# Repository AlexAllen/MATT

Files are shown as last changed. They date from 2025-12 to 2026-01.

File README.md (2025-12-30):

# Overview

MATT stands for "Multifunction Altimeter with Telemetry and Tracking", and is a DIY flight computer project that aims to tick several boxes in the [United Kingdom Rocketry Association's (UKRA) Model Achievement Program (MAP)](https://ukra.org.uk/certification/model-achievement-programme/). I have already done the DIY altimeter task, using an Arduino and breakout boards on stripboard, as recorded in [my rocket altimeter repo](https://github.com/AlexAllen/rocket_altimeter), and this project intends to produce something that can tick all of the remaining MAP tasks that require a custom altimeter:

* DIY flight computer
	* Details are light on the exact requirements, but I'm assuming a typical dual deploy flight computer
* Satellite
	* A cansat which records some physical data and transmits it back to the ground at 1Hz.
* Land under thrust
	* Need to be able to control servos for thrust vectoring

I also want to use this project as a vehicle for learning about PCB design, and to improve my electronics skills more generally. I intend to use a microcontroller board (maybe a Pico of some sort, or a Teensy) as a starting point, and then to create my own PCB to provide the rest of the functionality I require. I might do this in stages, creating some simpler boards with a subset of the final functionality on the way towards the final board. 

While the resulting flight computer will be overkill for any of these applications, as I don't expect space or weight contraints to be an issue for any of the flights (within reason), having them all use the same computer (or at least a subset of the same computer) means that every flight can help collect data and test functionality for each of the other applications. If I subsequently find I want a more compact, focussed flight computer for a specific application, then that can be its own project, building on the experience gained here. 

---------------------

# Requirements

1. Must have Mach safe two channel (apogee and main) deployment triggered off pressure data
	* Required to meet DIY flight computer task definition
1. Must have buzzer for audible altimeter arming alerts
	* Required for safety when completing DIY flight computer task
1. Must record flight data in a robust way in flight (not to an SD card!), and make the data retrievable afterwards
	* Will make the result more useful, and make it easier to test
1. Could have individual wireless test functionality for both deployment channels
	* Makes the result more flexible, but could be a later update
1. Must have UK legal radio link capable of transmitting recorded data at 1Hz
	* Required to meet Satellite task definition
1. Must record temperature data as well as pressure data, for transmission
	* Required for Satellite task
1. Should transmit on a frequency and in a format that can be picked up by an eggtimer USB ground station
	* Allows reuse of existing equiment
1. Must have enough PWM outputs to control a thrust vectoring mount and deploy legs
	* Required to meet the Land under thrust task task definition
1. Should have enough PWM outputs to control 4 canards instead of thrust vectoring and legs
	* Makes the result more future proof
1. Must have accelerometers and gyroscopes
	* Required to complete the Land under thrust task 
1. Should have magnetometers
	* Makes the result more flexible
1. Should have a GPS module, and be able to transmit as a GPS tracking radio
	* Makes the result more useful, given an onboard radio is required already
	
---------------------

# Potential chips/ boards to investigate

## Microcontroller

### Pimoroni Pico 2 Plus W / Pico LiPo 2 XL W

The Pico 2 Plus W was my starting point before I started looking at the Teensy alternatives. I already have some, and have used them at least a little, so that's a plus in their favour. They also either come with, or have options for coming with, some features I want already built in. This includes wifi, and some lipo functionality. It also has bluetooth, if I want to use that instead of wifi. 

The Pico LiPo 2 XL W has the lipo functionality built in already, and is longer as a result (76mm vs 51mm), but also comes with more pins. They are both 21mm wide.

Useful links:

* [Pimoroni Pico 2 Plus W](https://shop.pimoroni.com/products/pimoroni-pico-plus-2-w?variant=42182811942995)
* [Pimoroni LiPo Shim](https://shop.pimoroni.com/products/pico-lipo-shim?variant=32369543086163)
* [Pimoroni Pico LiPo 2 XL W](https://shop.pimoroni.com/products/pimoroni-pico-lipo-2-xl-w?variant=55447911006587)

### Teensy 4.0 or 4.1

This looks to have a significantly more powerful processor than a pico plus 2, and hardware floating point calculations, so I'll have plenty of grunt for calculations, but have to do more stuff myself (wifi, etc). The Teensy 4.1 is a larger and more fully featured board than the Teensy 4.0, at about 61mm vs 36mm (both are about 18mm wide). The 4.1 has the option to add 2x 8MB QSPI chips directly onto the board, and a built in microSD card reader, so I could look at writing some data storage/ retrival code before the PCB is complete.

Useful links:

* [Pi Hut Teensy 4.1](https://thepihut.com/products/teensy-4-1)
* [Pimoroni Teensy 4.1](https://shop.pimoroni.com/products/teensy-4-1?variant=31757218250835)
* [Teensy 4.1 documentation](https://www.pjrc.com/store/teensy41.html)

Or:

* [Pi Hut Teensy 4.0](https://thepihut.com/products/pjrc-teensy-4-0-usb-development-board)
* [Pimoroni Teensy 4.0](https://shop.pimoroni.com/products/teensy-4-0-development-board?variant=29443577217107)
* [Teensy 4.0 documentation](https://www.pjrc.com/store/teensy40.html)

## RF modules

### ESP8266-12 WiFi Module

If I go for the Teensy over the pico, then I don't get wifi built in. This is the wifi module that eggtimer uses.

### Hope RF HM-TRP-868 RF module

This is the one used by eggtimer, so should be compatible with the ground station. There is also an otherwise identical 433 MHz version, which may be useful later.

## Sensors

### BMP 390 (or 388, or 280, or ...)

A temperature and pressure sensor. I used the BMP 280 on my [rocket altimeter](https://github.com/AlexAllen/rocket_altimeter) with good results, and I have one on a breakout board to play with already. According to the Adafruit overview, the BMP280 has a relative accuracy of 12 Pa, the BMP388 8 Pa, and the BMP390 3 Pa. That translates to about 1m for the BMP280 or about 0.25m for the BMP390. Seems to be recommended on TRF threads about building flight computers, so this is probably the one to go for.

### LSM6DSV80X 

A two channel accelerometer, with gyroscope. 16g and 80g should cover most foreseeable use cases. The LSM6DSO32 or similar seem to be recommended on TRF, but this looks like an updated version that includes an 80g rather than a 32g high range accelerometer.

### LIS3MDL

This magnetometer is discussed on [TRF](https://www.rocketryforum.com/threads/magnetometer-calibration.193930/), but seems to be unavailable.

### LIS2MDLTR

This does appear to be available.

### Quectel L80-R

I have some of these, somewhere. Which is a big point in their favour!

### Something from ublox?

People seem to rate these highly, might be worth investigating

## Other

### VN5E160STR-E

These are what the eggtimer quark uses to control deployment charges. According to Cris Erving of Eggtimer Rocketry, ["in one SOIC-8 package you get 10A current limiting, continuity checking, brownout protection (it shuts off the load if the input voltage drops below 4.5V), overtemperature protection, and they will work with up to 40V input."](https://www.rocketryforum.com/threads/flight-computer-schematic-review-request.186506/post-2588670).

### W25Q01JVZEIM 

1 gigabit flash, so could store plenty of flight data, and recover it later, even after power off.

### Pololu D30V30MAL

Looks like a very capable buck converter.
	
---------------------

# Other useful things:

### Ulyu (Silicdyne) talks about how to implement an IMU

[This thread on TRF](https://www.rocketryforum.com/threads/did-any-one-found-out-a-way-to-calculate-the-velocity-and-altitude-using-imu-sensors-with-practical-code.191467/post-2722289)

### Cris Erving (Eggtimer) suggests owning this book

[The Circuit Designer's Companion](https://www.amazon.co.uk/Circuit-Designers-Companion-Wilson-Professor/dp/0081017642)

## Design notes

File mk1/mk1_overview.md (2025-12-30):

# Overview
## Summary

As a first go, I am going to leave out the wifi module, but include most of the other functionality, using sensors that I either already have, use elsewhere, or come recommended on TRF. 

## Major components

1x Teensy 4.1 with flash and psram 
1x Hope RF HM-TRP-868 RF module
	- Connect with UART
1x BMP 390
	- Connect with SPI
1x LSM6DSV80X
	- Connect with SPI
1x LIS2MDL
	- Connect with I2C
1x Quectel L80-R
	- Connect with UART
2x VN5E160STR-E for deployment charges
1x buzzer
4x pwm out
1x Pololu D30V30MAL

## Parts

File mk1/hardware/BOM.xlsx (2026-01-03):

Item # | Designator | Qty | Manufacturer | Mfg Part # | Description | Package/ Footprint | Type | Link | Instructions/ Notes
1 | U1 | 1 | www.pjrc.com | Teensy 4.1 | Microcontroller | 0.1" header, 24 pins down each side | thru-hole | https://www.pjrc.com/store/teensy41.html
2 | U2 | 1 | HOPERF | HM-TRP-869S | RF module | Surface mount PCB | SMD | https://www.tme.eu/gb/details/hm-trp-869s/rf-modules/hope-microelectronics/
3 | U3 | 1 | Bosch | BMP390 | Pressure sensor | 10-pin metal-lid LGA | SMD | https://www.mouser.co.uk/ProductDetail/Bosch-Sensortec/BMP390?qs=QNEnbhJQKvYQVfvRMgo2YA%3D%3D
4 | U4 | 1 | ST | LSM6DSV80XTR | Accelerometers and gyroscopes | LGA-14L | SMD | https://www.mouser.co.uk/ProductDetail/STMicroelectronics/LSM6DSV80XTR?qs=bN4HulGPsrFs7nx%2F3S8HMg%3D%3D
5 | U5 | 1 | Pololu | D30V30MAL | Buck regulator | 0.1" header, 6 pins, and M2 mounting hole | thru-hole | https://www.pololu.com/product/4873
6 | U6 | 1 | Quectel | L80-R | GPS module | Surface mount PCB | SMD | https://www.mouser.co.uk/ProductDetail/Quectel/L80RE-M37?qs=sGAEpiMZZMu3sxpa5v1qrlnBiwhQeiBhi9WeJRp64R0%3D
7 | U7, U8 | 2 | ST | VN5E160STR-E | High side driver | SO-8 | SMD | https://www.mouser.co.uk/ProductDetail/STMicroelectronics/VN5E160STR-E?qs=%252BB84zevwoRC5YUcxzPzBgA%3D%3D
8 | U9, U11, U12 | 3 | GCT | TBC05-04-1-G-G | Terminal block | 0.1" pins | thru-hole | https://www.mouser.co.uk/ProductDetail/GCT/TBC05-04-1-G-G
9 | U10 | 1 | ST | LIS2MDLTR | Magnetometer | LGA-12L | SMD | https://www.mouser.co.uk/ProductDetail/STMicroelectronics/LIS2MDLTR
10 | AE1 | 1 | Linx | ANT-868-PW-LP | Antenna | screw mount | screw mount | https://www.mouser.co.uk/ProductDetail/TE-Connectivity-Linx-Technologies/ANT-868-PW-LP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
11 | BZ1 | 1 | AATC | AX-1203D-LF | Piezo buzzer | 12mm diameter | thru-hole | https://www.mouser.co.uk/ProductDetail/AATC/AX-1203D-LF?qs=uwxL4vQweFOhu1GHny4ZQQ%3D%3D
12 | R1, R2, R3, R4 | 4 | YAGEO | RV0805JR-0710KL | 10k resistor | 0805 | SMD | https://www.mouser.co.uk/ProductDetail/YAGEO/RV0805JR-0710KL?qs=qpJ%252B%252B%252Bdg6p3bGiIDT3p%252B0w%3D%3D
13 | R5, R6 | 2 | YAGEO | AR0805JR-074K7L | 4.7k resistor | 0805 | SMD | https://www.mouser.co.uk/ProductDetail/YAGEO/AR0805JR-074K7L?qs=tub3WQyKOl8zx7%2F0DCfAlQ%3D%3D
14 | C1, C2, C3, C4, C5, C9, C11, C12, C13, C16 | 10 | KEMET | C0805C104J5RAC | 100nF capacitor | 0805 | SMD | https://www.mouser.co.uk/ProductDetail/KEMET/C0805C104J5RAC?qs=r%2FVmNO8Tjq7NnSJCDQvpIg%3D%3D
15 | C10, C15 | 2 | Walsin | 0805X106J100CT | 10uF capacitor | 0805 | SMD | https://www.mouser.co.uk/ProductDetail/Walsin/0805X106J100CT?qs=u16ybLDytRbl7URUhuT5XQ%3D%3D
16 | C14 | 1 | KEMET | C0805C224J1RACTU | 220nF capacitor | 0805 | SMD | https://www.mouser.co.uk/ProductDetail/KEMET/C0805C224J1RACTU?qs=JKO44DJ%252BG3gPbSqeZuvstQ%3D%3D

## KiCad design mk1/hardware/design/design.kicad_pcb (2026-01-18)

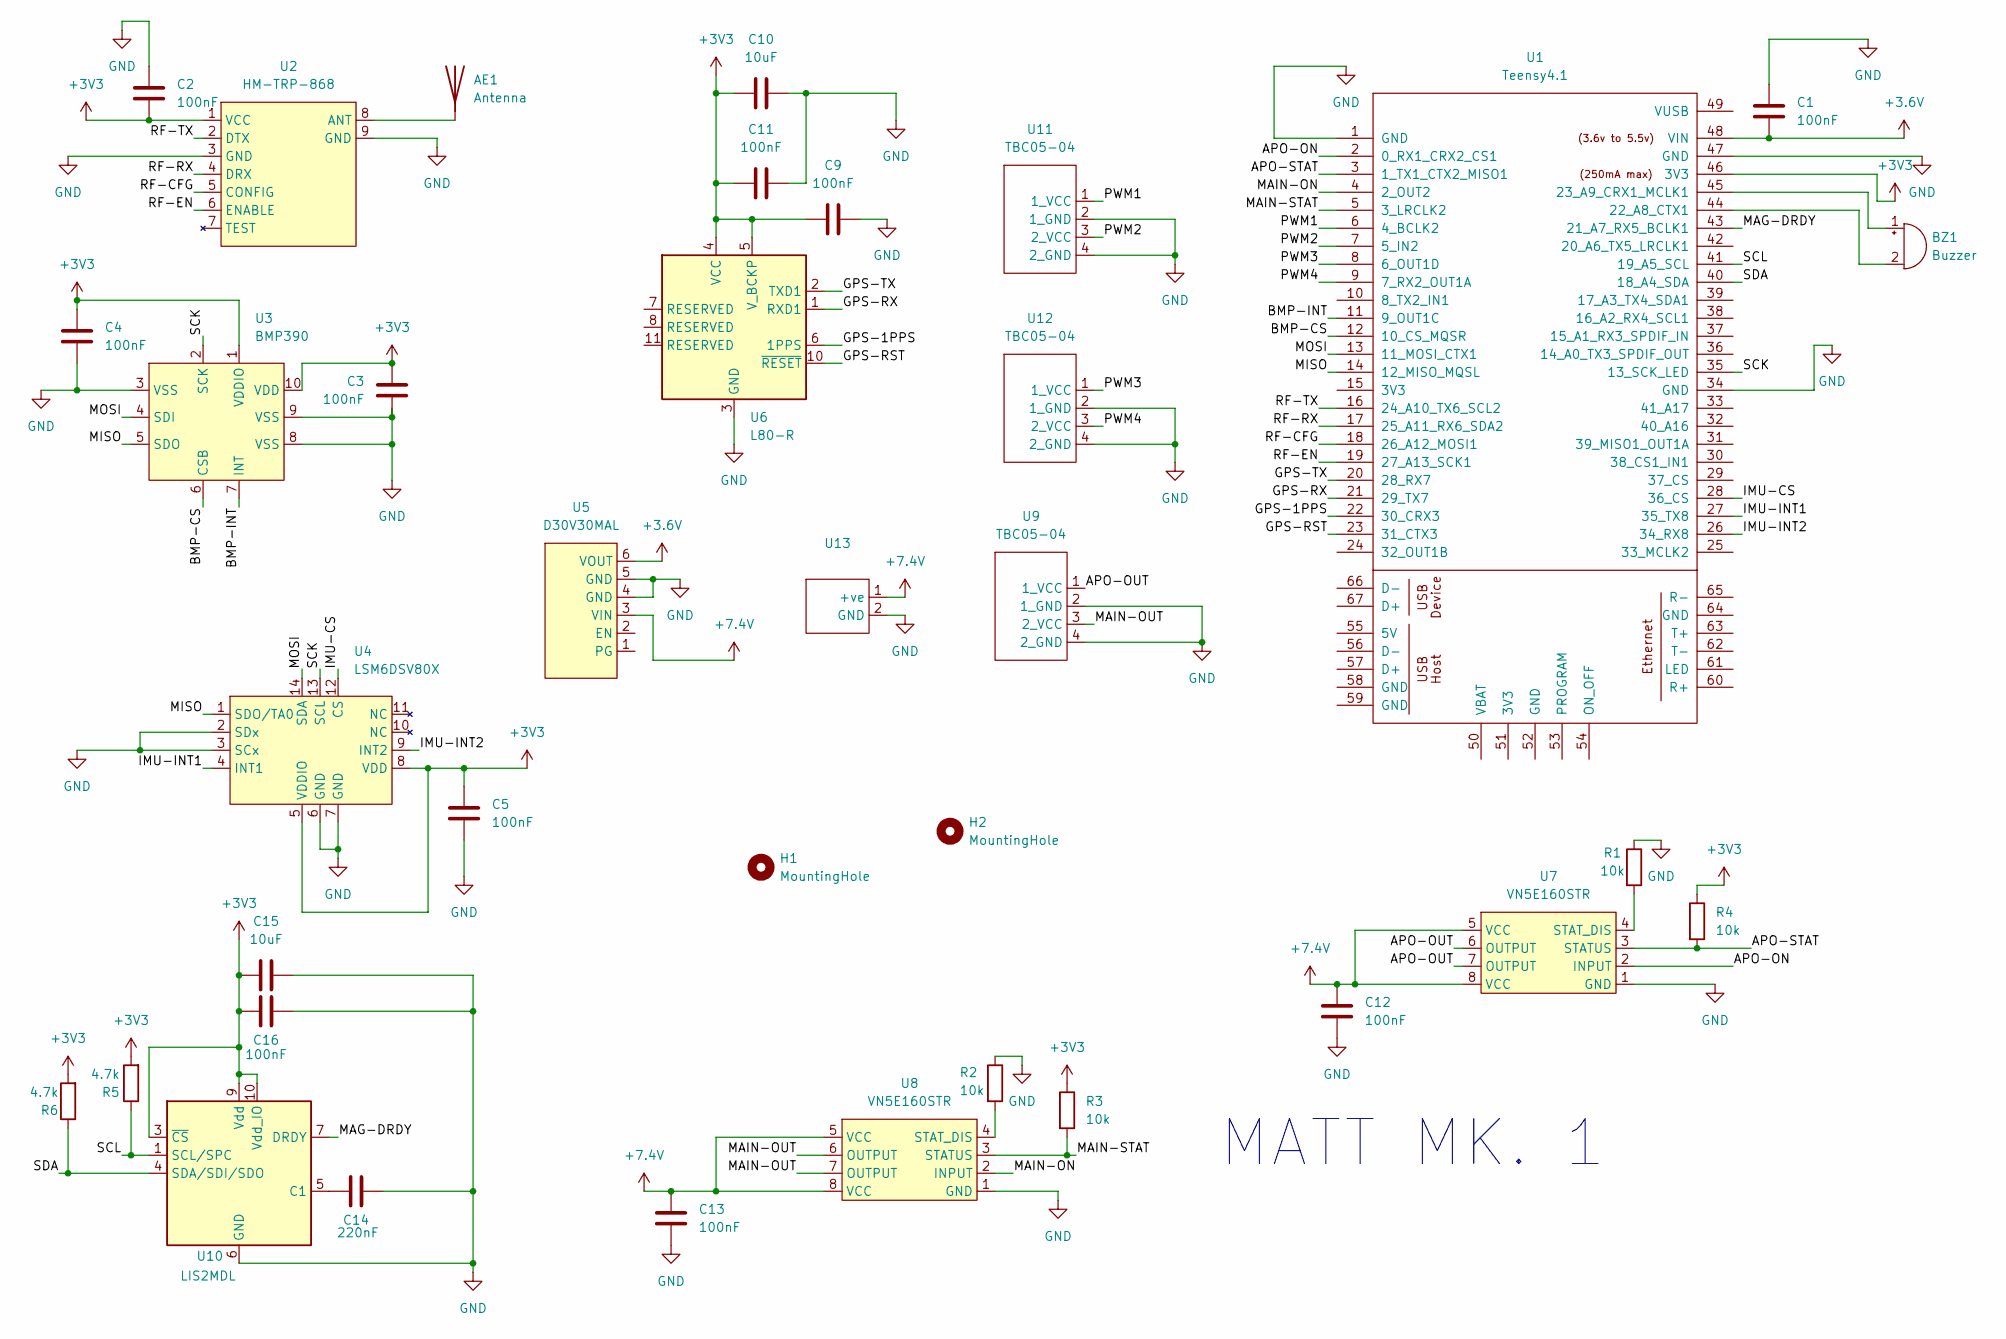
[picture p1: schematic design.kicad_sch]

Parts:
AE1: Antenna; ANT-868-PW
BZ1: Buzzer; AX1203DLF
C1, C2, C3, C4, C5, C9, C11, C12, C13, C16: 100nF; C_0805_2012Metric_Pad1.18x1.45mm_HandSolder
C10, C15: 10uF; C_0805_2012Metric_Pad1.18x1.45mm_HandSolder
C14: 220nF; C_0805_2012Metric_Pad1.18x1.45mm_HandSolder
H1, H2: MountingHole; MountingHole_2.7mm_M2.5
R1, R2, R3, R4: 10k; R_0805_2012Metric_Pad1.20x1.40mm_HandSolder
R5, R6: 4.7k; R_0805_2012Metric_Pad1.20x1.40mm_HandSolder
U1: Teensy4.1; teensy4.1
U2: HM-TRP-868; HM-TRP-XXX
U3: BMP390
U4: LSM6DSV80X
U5: D30V30MAL; D30V30MAx
U6: L80-R; Quectel_L80-R
U7, U8: VN5E160STR; vn5e160s
U9: TBC05-04; TBC05-04_charges
U10: LIS2MDL; LGA-12_2x2mm_P0.5mm
U11: TBC05-04; TBC05-04_pwm1
U12: TBC05-04; TBC05-04_pwm2
U13: power_in

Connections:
+3.6V: C1.1, U1.48 (VIN), U5.6 (VOUT)
+3V3: C2.2, C3.1, C4.1, C5.1, C9.2, C10.2, C11.2, C15.1, C16.2, R3.1, R4.1, R5.2, R6.2, U1.46 (3V3), U2.1 (VCC), U3.1 (VDDIO), U3.10 (VDD), U4.5 (VDDIO), U4.8 (VDD), U6.4 (VCC), U6.5 (V_BCKP), U10.3 (~CS), U10.9 (Vdd), U10.10 (Vdd_IO)
+7.4V: C12.1, C13.1, U5.3 (VIN), U7.5 (VCC), U7.8 (VCC), U8.5 (VCC), U8.8 (VCC), U13.1 (+ve)
/APO-ON: U1.2 (0_RX1_CRX2_CS1), U7.2 (INPUT)
/APO-OUT: U7.6 (OUTPUT), U7.7 (OUTPUT), U9.1 (1_VCC)
/APO-STAT: R4.2, U1.3 (1_TX1_CTX2_MISO1), U7.3 (STATUS)
/BMP-CS: U1.12 (10_CS_MQSR), U3.6 (CSB)
/BMP-INT: U1.11 (9_OUT1C), U3.7 (INT)
/GPS-1PPS: U1.22 (30_CRX3), U6.6 (1PPS)
/GPS-RST: U1.23 (31_CTX3), U6.10 (~RESET)
/GPS-RX: U1.21 (29_TX7), U6.1 (RXD1)
/GPS-TX: U1.20 (28_RX7), U6.2 (TXD1)
/IMU-CS: U1.28 (36_CS), U4.12 (CS)
/IMU-INT1: U1.27 (35_TX8), U4.4 (INT1)
/IMU-INT2: U1.26 (34_RX8), U4.9 (INT2)
/MAG-DRDY: U1.43 (21_A7_RX5_BCLK1), U10.7 (DRDY)
/MAIN-ON: U1.4 (2_OUT2), U8.2 (INPUT)
/MAIN-OUT: U8.6 (OUTPUT), U8.7 (OUTPUT), U9.3 (2_VCC)
/MAIN-STAT: R3.2, U1.5 (3_LRCLK2), U8.3 (STATUS)
/MISO: U1.14 (12_MISO_MQSL), U3.5 (SDO), U4.1 (SDO/TA0)
/MOSI: U1.13 (11_MOSI_CTX1), U3.4 (SDI), U4.14 (SDA)
/PWM1: U1.6 (4_BCLK2), U11.1 (1_VCC)
/PWM2: U1.7 (5_IN2), U11.3 (2_VCC)
/PWM3: U1.8 (6_OUT1D), U12.1 (1_VCC)
/PWM4: U1.9 (7_RX2_OUT1A), U12.3 (2_VCC)
/RF-CFG: U1.18 (26_A12_MOSI1), U2.5 (CONFIG)
/RF-EN: U1.19 (27_A13_SCK1), U2.6 (ENABLE)
/RF-RX: U1.17 (25_A11_RX6_SDA2), U2.4 (DRX)
/RF-TX: U1.16 (24_A10_TX6_SCL2), U2.2 (DTX)
/SCK: U1.35 (13_SCK_LED), U3.2 (SCK), U4.13 (SCL)
/SCL: R5.1, U1.41 (19_A5_SCL), U10.1 (SCL/SPC)
/SDA: R6.1, U1.40 (18_A4_SDA), U10.4 (SDA/SDI/SDO)
GND: C1.2, C2.1, C3.2, C4.2, C5.2, C9.1, C10.1, C11.1, C12.2, C13.2, C14.2, C15.2, C16.1, R1.1, R2.1, U1.1 (GND), U1.34 (GND), U1.47 (GND), U2.3 (GND), U2.9 (GND), U3.3 (VSS), U3.8 (VSS), U3.9 (VSS), U4.2 (SDx), U4.3 (SCx), U4.6 (GND), U4.7 (GND), U5.4 (GND), U5.5 (GND), U6.3 (GND), U6.12 (GND), U7.1 (GND), U8.1 (GND), U9.2 (1_GND), U9.4 (2_GND), U10.6 (GND), U10.8 (GND), U11.2 (1_GND), U11.4 (2_GND), U12.2 (1_GND), U12.4 (2_GND), U13.2 (GND)
unnamed: AE1.1 (A), U2.8 (ANT)
unnamed: BZ1.1 (+), U1.45 (23_A9_CRX1_MCLK1)
unnamed: BZ1.2 (-), U1.44 (22_A8_CTX1)
unnamed: R1.2, U7.4 (STAT_DIS)
unnamed: R2.2, U8.4 (STAT_DIS)
unnamed: C14.1, U10.5 (C1)

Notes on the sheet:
MATT MK. 1

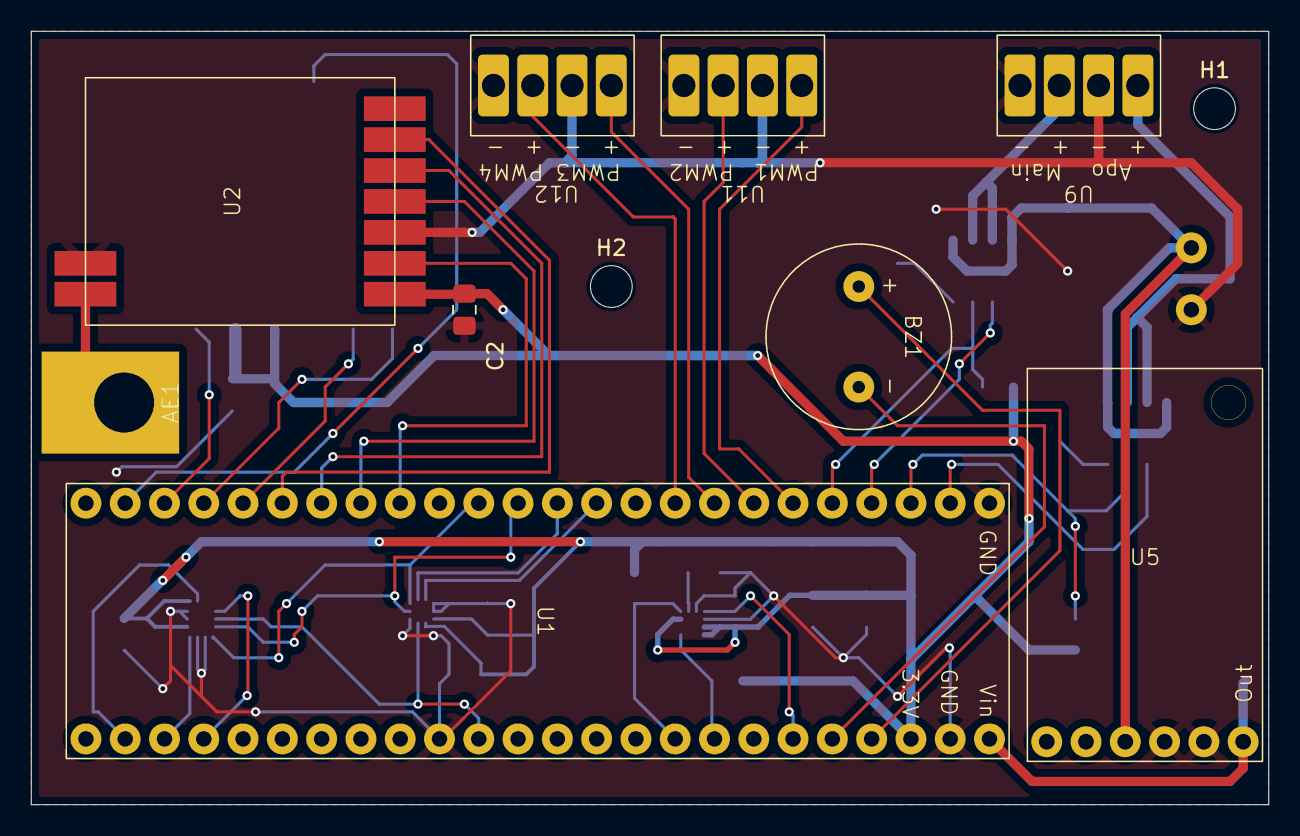
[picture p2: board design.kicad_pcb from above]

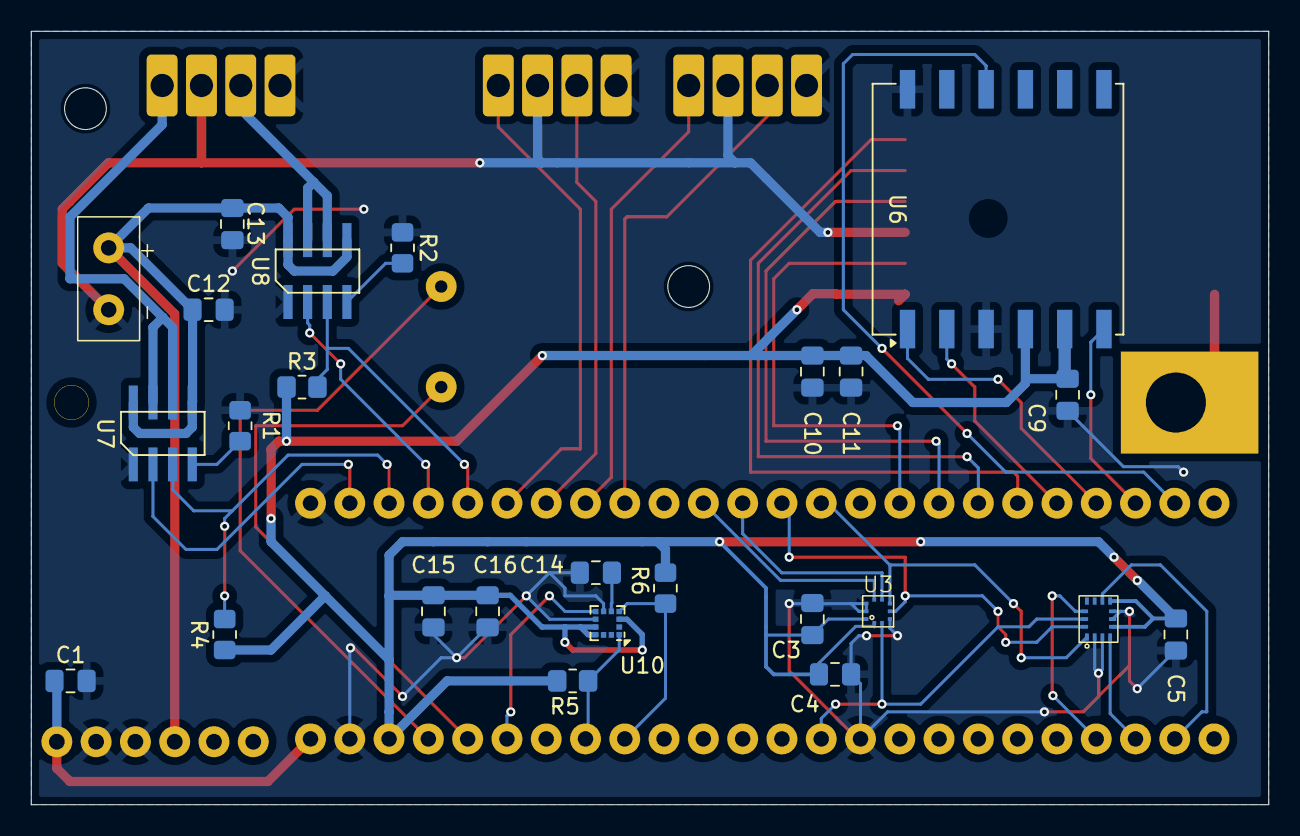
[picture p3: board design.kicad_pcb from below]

Board: 2 copper layers, 80.0 x 50.0 mm, 36 parts (25 on the bottom side), 39 nets.

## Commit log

2025-12-20 Add magnetometer to readme
2025-12-26 Add mk1 board schematic
    [design.kicad_pcb, design.kicad_sch]
2025-12-30 Updated schematic to use different (available) magnetometer
    [design.kicad_sch]
2025-12-31 Added symbol table, fixed magnetometer wiring
    [design.kicad_sch]
2026-01-01 Added footprints
    [design.kicad_sch]
2026-01-02 Add BOM and make a start at giving everything a suitable footprint
    [BOM.xlsx, design.kicad_sch]
2026-01-03 Picked antenna for BOM and added footprint
    [BOM.xlsx, design.kicad_sch]
2026-01-03 Add a few missing in and outputs, try to join up pins
    [BOM.xlsx, design.kicad_sch]
2026-01-07 First pass at PCB
    [design.kicad_pcb, design.kicad_sch]
2026-01-07 Close kicad before committing!
2026-01-07 Increase voltage regulator pad size
    [design.kicad_pcb]
2026-01-08 Added mounting holes
    [design.kicad_pcb]
2026-01-12 Thickened power traces, and tidied up a few sections. Still a bunch of design rule errors to work through
    [design.kicad_pcb]
2026-01-18 Fixed errors and some warnings
    [design.kicad_pcb, design.kicad_sch]
